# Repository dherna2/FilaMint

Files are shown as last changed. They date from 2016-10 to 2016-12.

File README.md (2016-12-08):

# FilaMint Team4

## This github was created for ECE411 Practicum Fall 2016  

### Collaborators are:

Colleen Nhim  
Nettaly Rebolledo  
David Hernandez  
Srijana Sapkota  

We used [Google drive] to simultanelously work on documents.  
Our finished documents have been transferred to the [Wiki](../../wiki) or saved in the folder named documents. 

[Google drive]: https://drive.google.com/drive/u/1/folders/0B7ei5UTStXl6bGFZWWxhMDdIQzQ

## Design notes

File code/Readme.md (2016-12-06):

Notes about wire connections to arduino, sensors with boards and prototype/Filamint board.  

gnd: hum(furthest pin right with holes facing up next to empty pin), lcd ("G" written on LCD board)

5v: hum(furthest pin left with holes facing up next to signal pin) , lcd ("P" written on LCD board)

Arduino 2 - hum_sig-resistor (2nd pin from left with holes facing up) - 328p pin4  
Note prototype is model after board which has digital pin 0 and 2 shorted

Arduino 8 - HX711 SCK -  328p pin14  

Arduino A3 - HX711 data - 328p pin26  

Arduino A5 - SCL ("L" written on LCD board) - 328p pin28 

Arduino A4 - SDA ("D" written on LCD board) - 328p pin27

Also Need to have the library for LCD installed, adafruit sensors, HX711  

Note for filamint board connectors have + for vcc and - for gnd helps with connector orientation

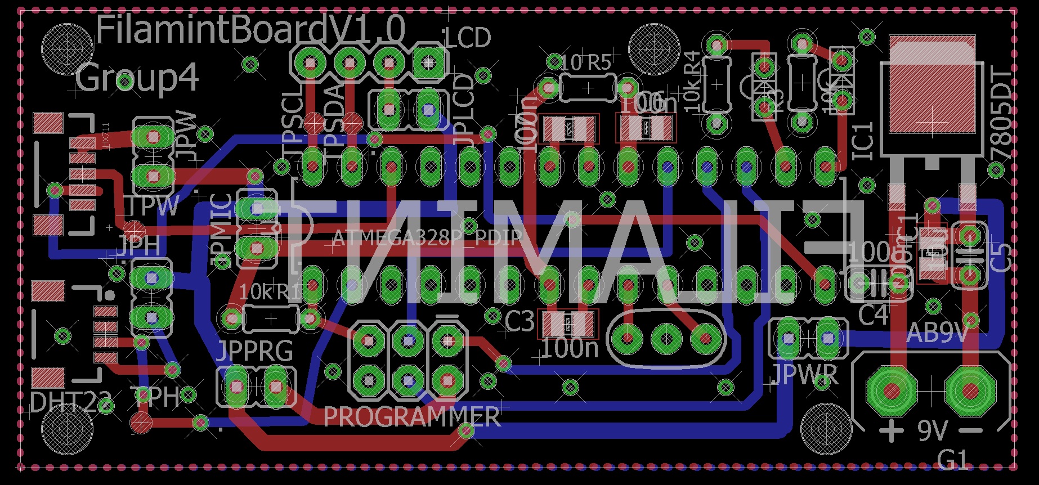
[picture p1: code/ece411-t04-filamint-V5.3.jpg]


[logo]: https://github.com/dherna2/FilaMint/blob/master/code/ece411-t04-filamint-V5.3.jpg "Homer is awsome"

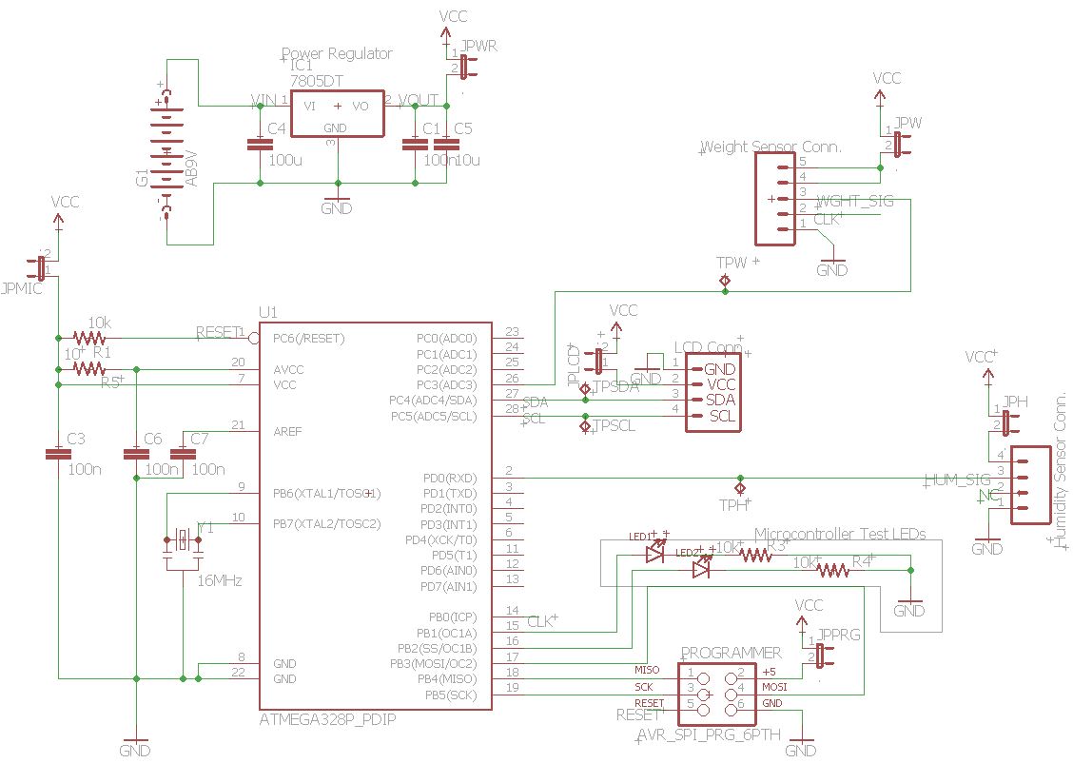
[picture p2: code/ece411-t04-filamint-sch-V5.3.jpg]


[logo2]: https://github.com/dherna2/FilaMint/blob/master/code/ece411-t04-filamint-sch-V5.3.jpg "Homer is awsome"

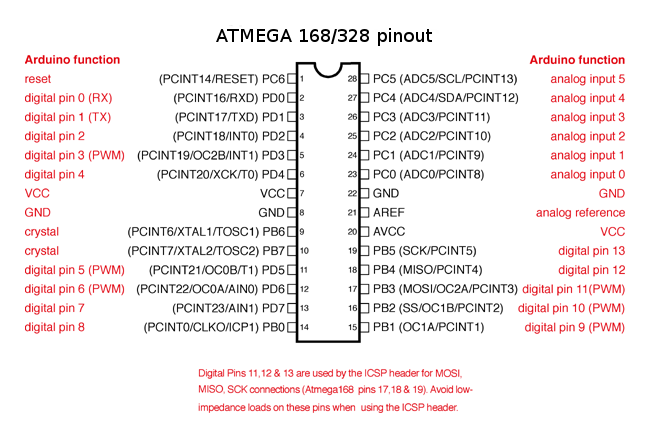
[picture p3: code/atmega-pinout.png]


[logo3]: https://github.com/dherna2/FilaMint/blob/master/code/atmega-pinout.png "Homer is awsome"

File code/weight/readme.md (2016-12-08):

## hx711 board connection  

The four wires coming out from the wheatstone bridge on the load cell are usually:  
•Excitation+ (E+) or VCC is red  
•Excitation- (E-) or ground is black  
•A-, O- or S- is green or blue  
•Amplifier+ (A+), Output+ (O+) or Signal+ (S+) is white

HX711 board -> Arduino 
GND-> GND  
DT->A1  
SCK->A0  
VCC-> 5v

Need to save this folder into your arduino library folder dont need test folder.
[Load Cell Library Source bogde](https://github.com/bogde/HX711)

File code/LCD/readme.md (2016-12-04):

## Wire Connection  

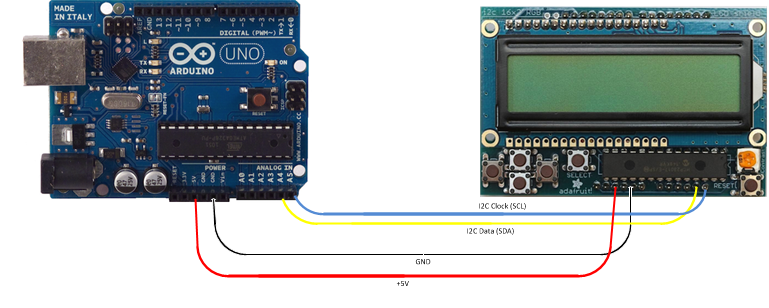
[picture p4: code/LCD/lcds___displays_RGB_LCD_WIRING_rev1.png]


[logo]: https://github.com/dherna2/FilaMint/blob/master/code/LCD/lcds___displays_RGB_LCD_WIRING_rev1.png "Homer is awsome"

Need to unzip file and save it in your arduino library folder  

Further details on use see adafruit tutorial [Using the RGB LCD Shield](https://learn.adafruit.com/rgb-lcd-shield/using-the-rgb-lcd-shield)

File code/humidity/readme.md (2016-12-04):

## Wire Connection  

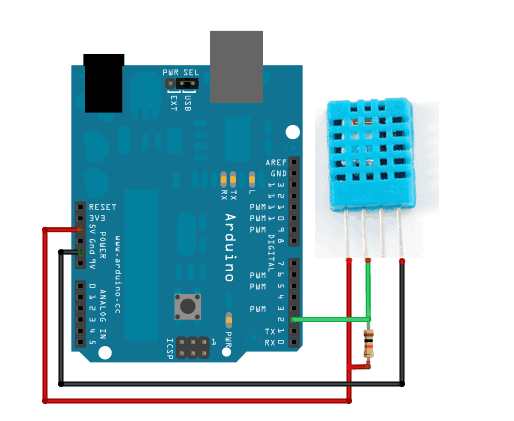
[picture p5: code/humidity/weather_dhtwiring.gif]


[logo]: https://github.com/dherna2/FilaMint/blob/master/code/humidity/weather_dhtwiring.gif "Homer is awsome"

Need to unzip both files and save them in your arduino library folder  

Further details on use see adafruit tutorial [Using a DHTxx Sensor](https://learn.adafruit.com/dht/using-a-dhtxx-sensor)

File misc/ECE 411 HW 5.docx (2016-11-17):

ECE 411

Homework 5

Group 4

# UML Physical View

→ → →

## USER

Box

Fridge

Nurse

## COMMUNICATION

## DATABASE

Compare values against server

Store values

Temp

ID/Patient/Vaccine

Date

## SERVER

Alarm text

UML Case Description

Use-Case | Activate temperature sensor
Actors | Customer, database, server
Description | The use-case occurs when a new temperature sensor is installed. Once installed, the server prompts the customer to add information, and check whether they have a subscription. If they don’t, the server prompts for payment information. If they do, then the sensor gets activated.
Stimulus | Costumer purchases a new sensor, then installs it into the fridge.
Response | Verify information, trigger monitor.

# UML Interaction View

5) Notify

Database

Sensor

Server

Comm

1) Wake up 3) Inquire →
2) Check temp → 4) Validity →

# HTTP GET String

http://www.vaccine.com/test/tempr_form.asp?name1=filamint_clinic&temp=98

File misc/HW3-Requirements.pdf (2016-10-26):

# FilaMint Requirements

# Group 4

## ECE 411 Version 2.0

FilaMint | 1

## Need

Filament is often improperly stored, which exposes the material to moisture. This exposure to moisture deteriorates the quality of the filament, therefore deteriorating the quality of the user’s print job. Additionally, printers normally will tell you how much filament has been used, but there is usually no way for the printer to measure how much filament is remaining on the spool. Both these issues lead to printing failures. There had to be a solution to fix these common issues for 3D printing enthusiasts. Because this market is starting to become affordable to all, FilaMint was created to become the affordable solution.

## Objective

The objective is to create an inexpensive device that will alert the customer if the storage humidity level is too high as well as when the filament is running low. The system must monitor humidity, alert user if humidity is too high, securely store filament in the enclosed and sealed container, and estimate how much filament is remaining.

## Background

A simple google search has shown that there have been similar designs that were created to prevent humidity from getting into the filament, but none that incorporate humidity and weight measurements in the same design. Some designs used a modified ‘air tight storage tote’ or a large ziplock bag that was then vacuum sealed. These designs were very low cost but didn’t alarm when humidity levels were too high. Some more expensive designs ($150+) looked like a modified desiccator oven that fits filament spools and it was able to regenerate desiccant packs, but this design did not monitor humidity levels or alarms. None of these designs measured the weight of the filament either.

## Requirements

### Functionality

- System must detect humidity within the container and alert the user if humidity is too high
- System must measure weight of the filament and alert the user if the filament is too low
- System must have an interface so the user can select type of filament they are storing
- The container must be sealed in order to reduce humidity

### Performance

- The weight measurement accuracy must be within 1 gram at all times
- The humidity sensor accuracy must be within 5% at all times
- The container must be able to store at least one spool of filament
- Information must be visible within 5 seconds when prompted

### Manufacturability

- The system must be manufactured on a circuit board with linear dimensions no less than 2cm and not greater than 30cm
- The system must be manufactured using two-layer printed circuit board technology

### Operational

- The system must be able to be able to operate in typical indoor environments (non-extreme).
- Must be used on a flat surface

### Economic

- Unit cost of less than $150
- Affordable unit
- The only maintenance cost must be the replacement of batteries.
- Must maintain silica beads

### Energy

- Must have replaceable power supply
- Supply must last a minimum of a month on standby

### Health & Safety

- Must not explode
- Must not emit unhealthy amounts of radiation
- System must not exceed ten pounds

### Legal

- Non-infringing patents and copyrights

### Environmental

- At least 50% of the components will be recyclable

### Maintainability

- User maintainable
- Product hardware components can be bought from at least 2 vendors

### Reliability & Availability

- MTTF 5 years

### Social & Cultural

- Must be easy to use and maintain by technical and non-technical users
- Intuitive and self-explaining

### Usability

- No on-site or user customization necessary or programming
- No longer than 30 minutes to learn how to use product
- Straightforward user interface with no more than 5 levels of menu options

### Documentation

- Instructions on the side explaining how to replace or recharge silica beads
- Instructions on how to use product

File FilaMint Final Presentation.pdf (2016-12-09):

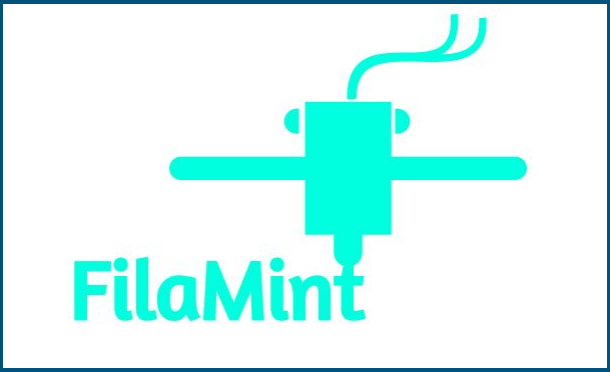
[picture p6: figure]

Portland State University
Group 4
Colleen Nhim, David Hernandez, Nettaly Rebolledo, Srijana Sapkota

# Background

# Solution

Project We wanted to create a product that would safely store filament in a way that prevent exposure to moisture. Warnings for high humidity and low filament.

Importance Keeping filament unexposed to moisture will preserve the quality of the filament, therefore maintaining the quality of the print job and success rate. The product will also let the user know how much filament is remaining so they are not risking the chances of running out of filament mid print. This product is crucial to successful print jobs.

# Objective

Filament is often kept unstored leaving exposure to moisture. Printers tell you how much you’ve printed but not how much filament is left in a spool. This product fixes both of these issues to increase the success and quality of a print job.

Our goal is to create a working prototype to pair with a 3D printer.

# Alternatives

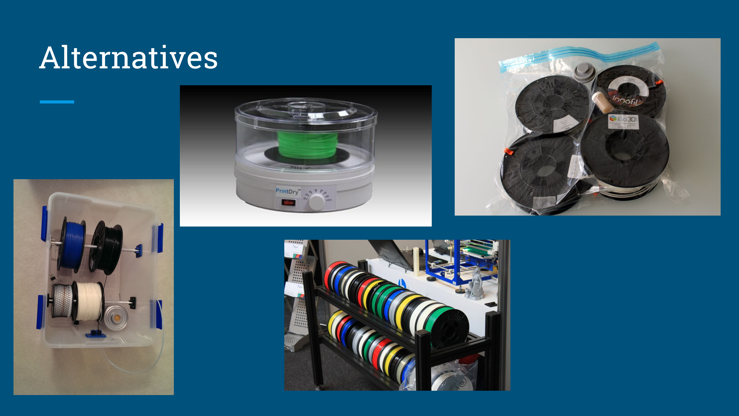
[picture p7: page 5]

# Requirements

## Functionality

- System must detect humidity within the container and alert the user if humidity is too high
- System must measure the length of the filament and alert the user if the filament is too low
- System must have an interface so they can get the readings from the container
- The container must be sealed in order to reduce humidity

# Requirements

## Performance

- The weight measurement accuracy must be within 1 gram at all times
- The humidity sensor accuracy must be within 5% at all times
- The container must be able to store at least one spool of filament
- Information must be visible within 5 seconds when prompted

# Approach

-Wanted to be cost effective

-Not take up a lot of space

-Accurate measurements and calculations

# Design: Hardware

# Black Box

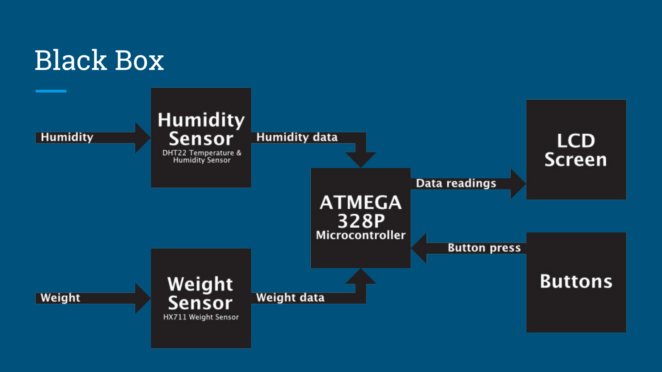
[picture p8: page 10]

# Event Table

EVENT | TRIGGER | PROCESS | SOURCE
Display readings | Button press | Data read | User
High humidity alert | Humidity readings | Display alert on LCD screen | System
Low filament warning | Remaining length reading | Display alert on LCD screen | System

# Hardware

1. Load cell - weight sensor
- To measure weight of filament spool
- Load cell is a transducer that translates force/ pressure into electric signal.
- Bar Strain gauges: Two wired organized wires where resistance changes upon stretching/ compressing
- Force sensed by deformation of strain gauge(s)
- Bar strain gauge load cell (Z-shape) (provides torque for easier and accurate measurement)

# Hardware

2. HX711 - Load cell Amplifier breakout board
- Load cell amplifier to read load cells to measure weight.
- Reads in small change in resistance and we can measure accurate weight with some calibration.
- Wheatstone bridge configuration used by load cell to connect to HX711
- Load cell has 4 strain gauges hooked up in wheatstone bridge formation (takes small change in resistance and make it more measurable)

# Hardware

3. DHT22 - Humidity Sensor
- Low cost temperature and humidity sensor
- Uses capacitive humidity sensor to measure surrounding air
- Use pullup resistor from data pin to Vcc.

# Hardware

4. LCD
- LCD Shield Kit w/ 16x2 Character Display
- I2C communication uses only 2 pins to connect with microcontroller
- 5 keypad buttons built-in the LCD
- Blue and White colors
- Backlight

# Hardware

5. ATMega328P-PU - Microcontroller and SMD components
- Low cost microcontroller
- Similar to Arduino Uno - used for Development
- 8 bit AVR, 32 ch, 23 GPIO
- External 16 MHz Resonator with Built in Capacitor
- 100nF SMD Capacitor in 805 packaging
- LM340S Line 5v Voltage Regulator
- 4 pin SMD connector and ribbon cables

# Design: Software

Software and Misc.

C - Language using Arduino

- Humidity and LCD libraries were downloaded from purchaser Adafruit.
- HX711 library was downloaded from github after finding one that worked
- Combined the examples together to form our code

Misc

- ¼ in. Acrylic sheets for support and durability
- 4xAA battery holder to provide long life

# Implementation

# Components

-Humidity Sensor: Analog to digital humidity and temperature sensor

-Weight Sensor: Weighs the spool

-Microcontroller: Controls the circuit

-LCD Display: Displays readings and menu

-Acrylic: The container

-Silica beads: Used to maintain low humidity levels

-Plexiglass: Sheets put together to make shell

# Bill of Materials

Part | Quantity | Price (including shipping)
Microprocessor | 1 | $5.00
Humidity Sensor | 1 | $7.00
Blue and White LCD kit | 1 | $25.00
4xAA Battery Pack | 1 | $2.92
HX711 Board | 1 | $2.93
Plexiglass sheets ($9 ea) | 3 | $27.00
Misc hardware (i.e. screws, hinges, etc) | 1 | $10.00
| | Total: $79.85

# Tools Used

- Arduino used for Development
- Eagle CAD used for schematic and board layout
- Laser cutter for plexiglass
- Drill press for screw holes

# Test Cases

Test Case Link (https://docs.google.com/a/pdx.edu/spreadsheets/d/1ZcRj_BzytFNqw8m9PkoywJ23xHQr0xwOn_bJI6cZJ2M/edit?usp=sharing)

# Schematic

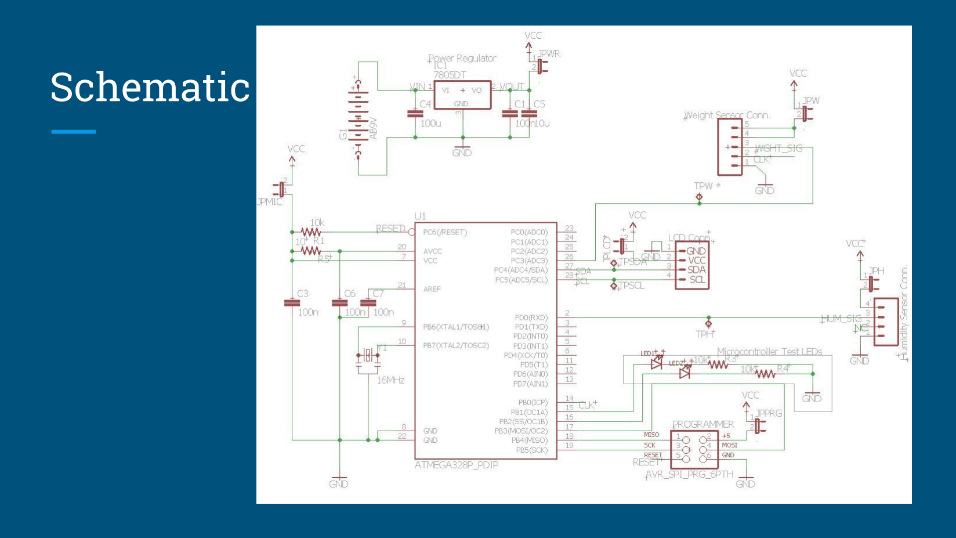
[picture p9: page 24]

# Board Layout

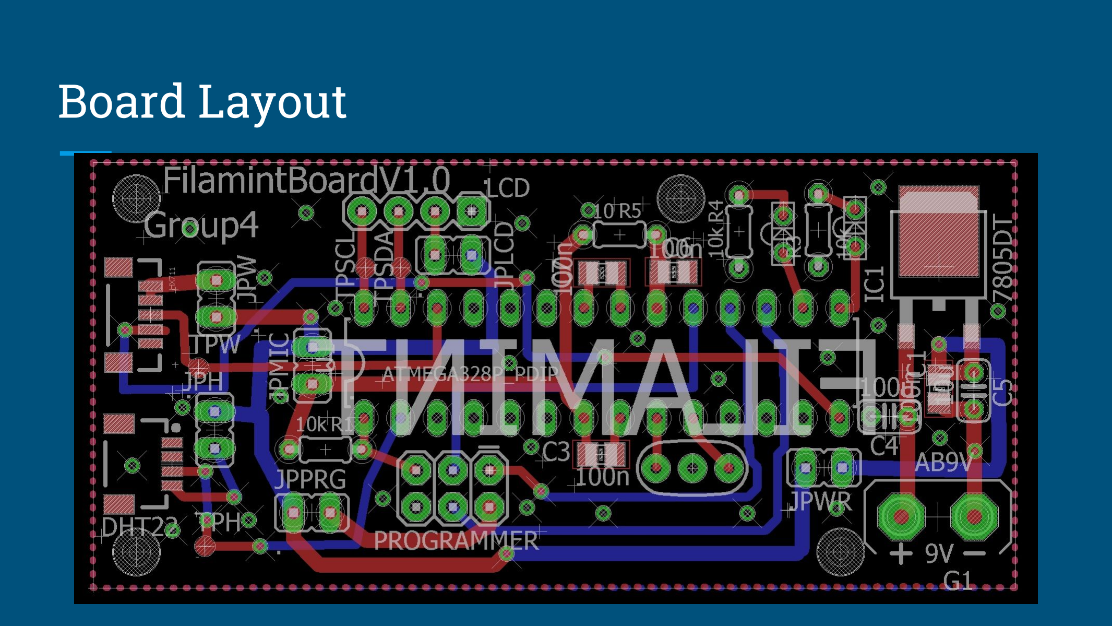
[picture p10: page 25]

# Prototype Board

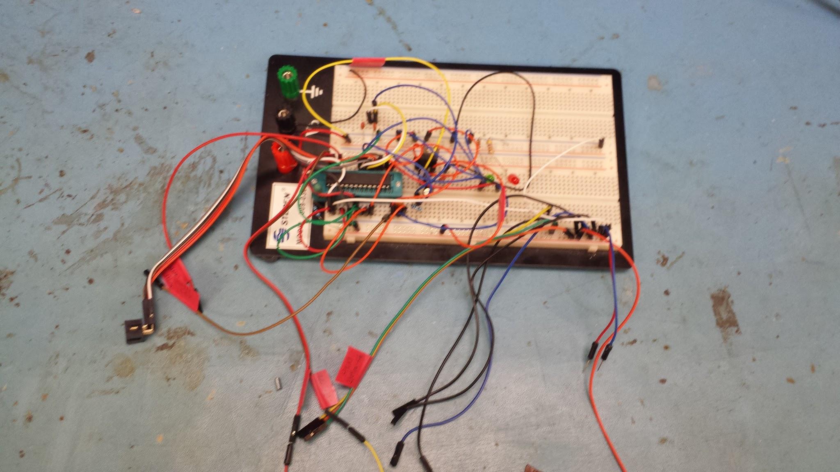
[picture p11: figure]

# Code

-Mass to Length conversion equation

-User Interface menu

-Displays and warns of high levels of humidity and low filament length

# Code

- Github (https://github.com/dherna2/FilaMint/blob/master/code/filamint_code/FilaMintVer12.ino)

# IP and Prior Work

# Referenced Work

- Used purchaser’s Libraries, example code and tutorials
- LCD - Adafruit
- Humidity - Adafruit
- Weight - open source code from github user bogde

# Testing

# Strategy for Testing

- Solder board and parts together
- Upload code to board
- Debug

# Results

# What worked?

- Team meetings - accomplished a lot together in a short amount of time
- Google Drive to simultaneously work on documents
- GitHub to share code, create helpful pages, and revision control
- Locker with easy to remember combo “MINT” to keep all items at school
- Google Hangouts to create a dedicated group chat with all members this helped with status reports, questions, tips, notes, accountability
- LID and capstone lab tools i.e. laser cutter, drill press, crimper, dremel, etc.
- Extra parts purchased (we got some bad parts and slow shipping)

# What didn’t work?

- Example codes - found out some example codes were outdated
- SMD connectors and ribbon cables are difficult to work with
- Group decisions on small items took longer than expected
- Learning curve was long for new tools i.e. github, eagle cad, arduino, atmel_studio, SMD soldering, LID tools-laser cutter, reflow oven

# Individual Contributions

Colleen: coding, laser cutting, assembly, calculations/conversions, filament

David: construction, assembly, coding, debugging, EagleCAD design

Nettaly: debugging, coding, design, circuit analysis

Srijana: board layout, assembly, coding, laser cut, documentation

# Lessons Learned

-What did each member learn

-what would we do differently

- More peer reviews
- Dedicated roles with backup
- More communication

-If we had more time…

- Better menu

-biggest mistake

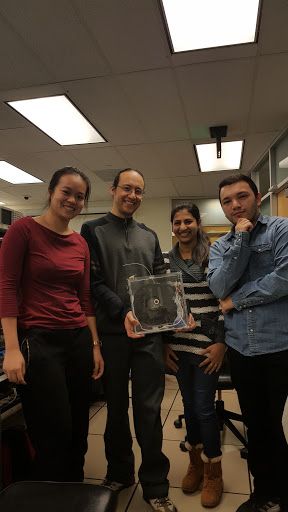
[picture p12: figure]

# Live demonstration!!

Thank you!

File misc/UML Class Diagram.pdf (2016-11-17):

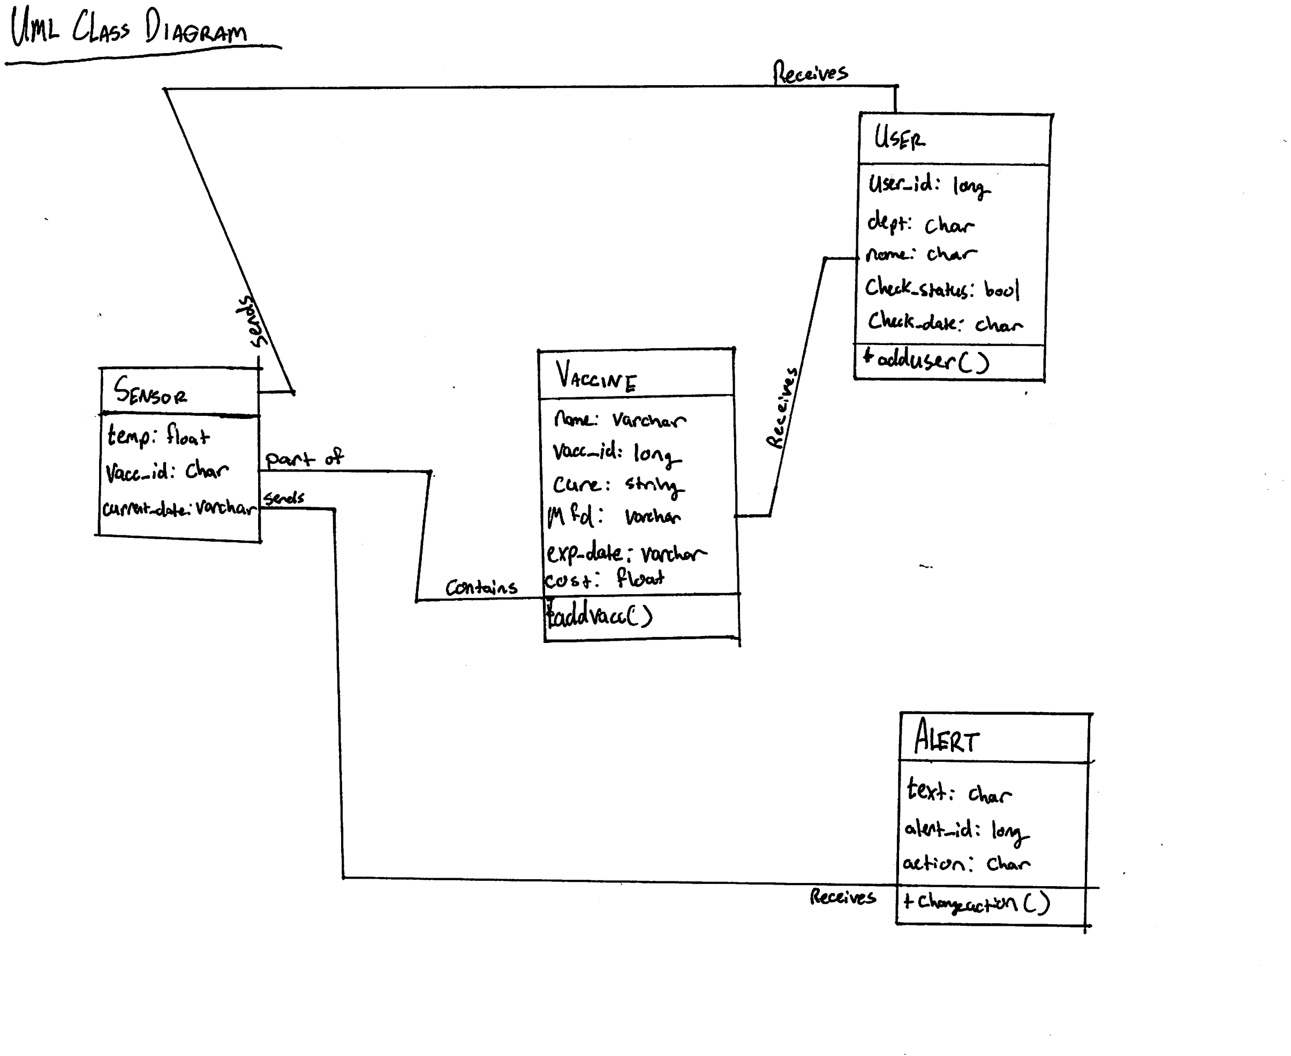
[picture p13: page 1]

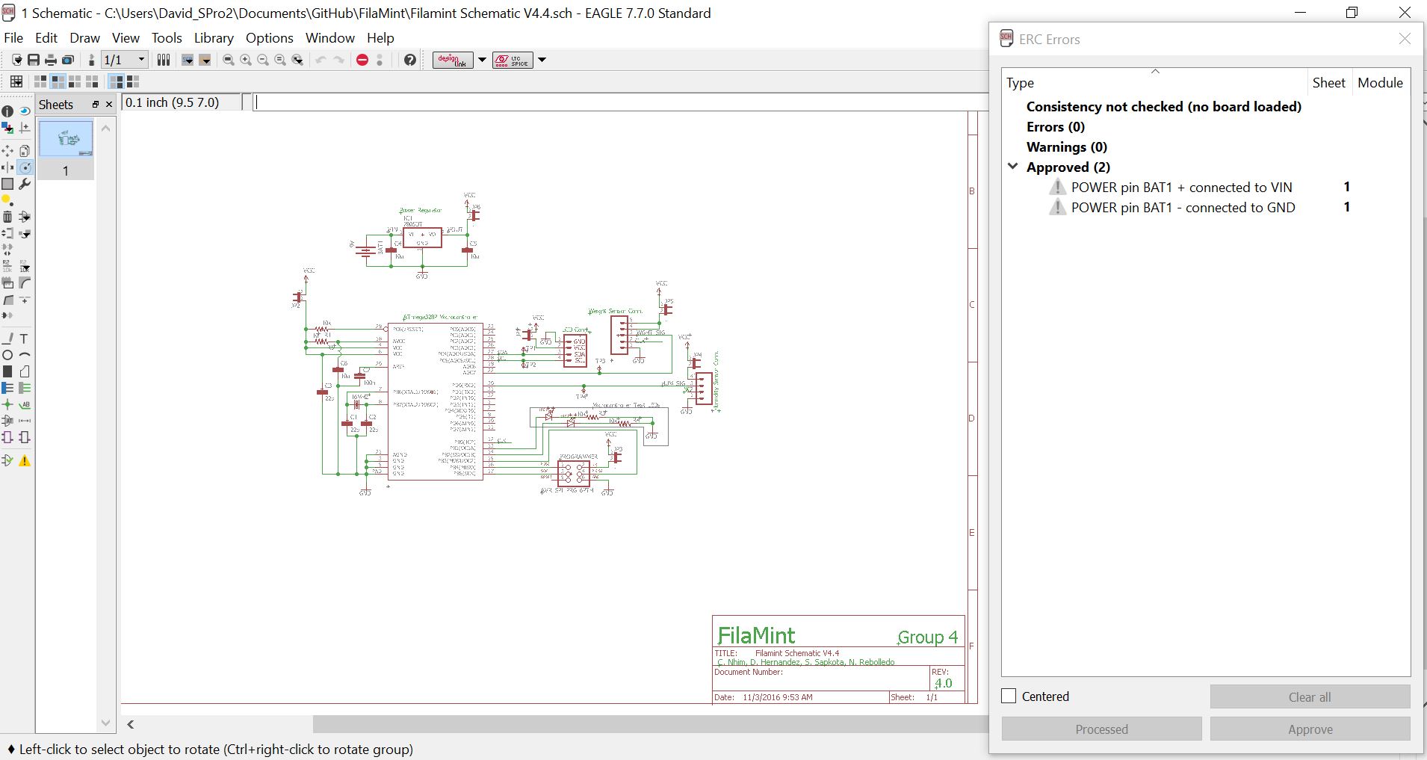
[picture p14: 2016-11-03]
Schematic/Filamint Schematic V4.4_ERC.JPG

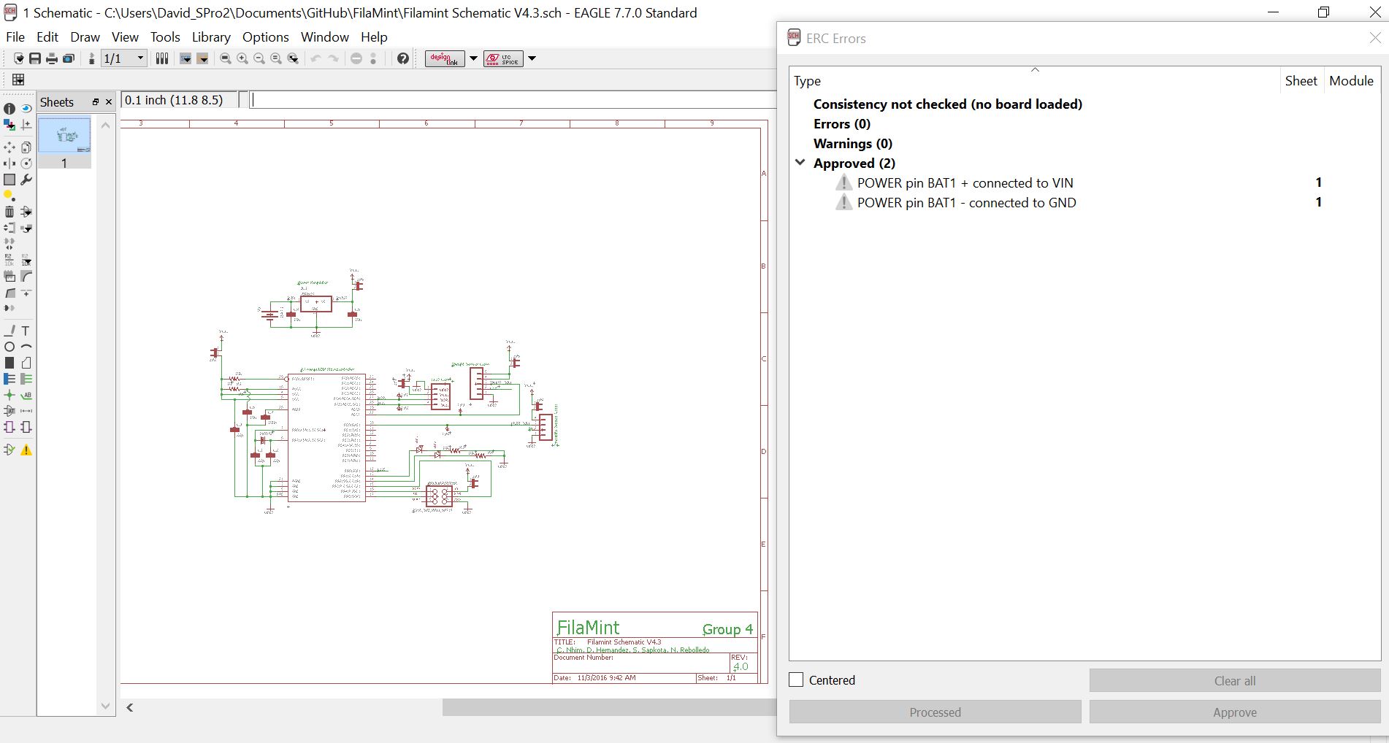
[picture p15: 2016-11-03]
Schematic/Filamint Schematic V4.3_ERC.JPG

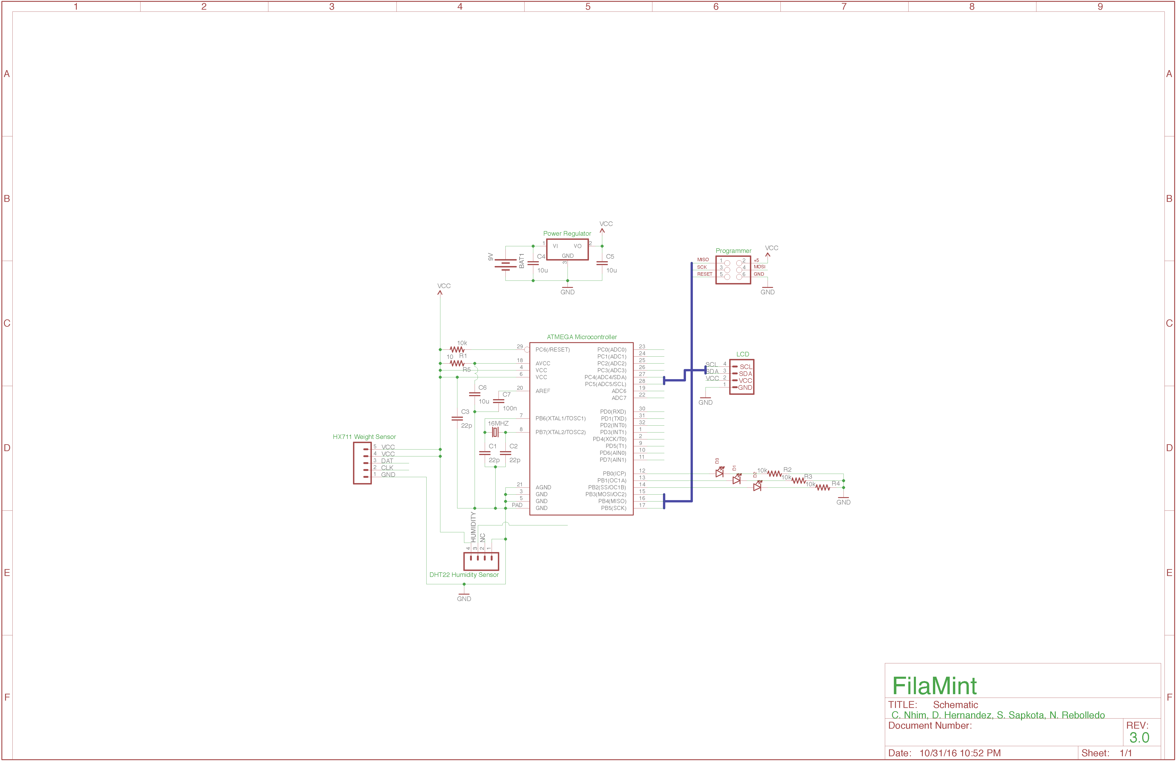
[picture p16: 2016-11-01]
Schematic/Filamint Schematic.png

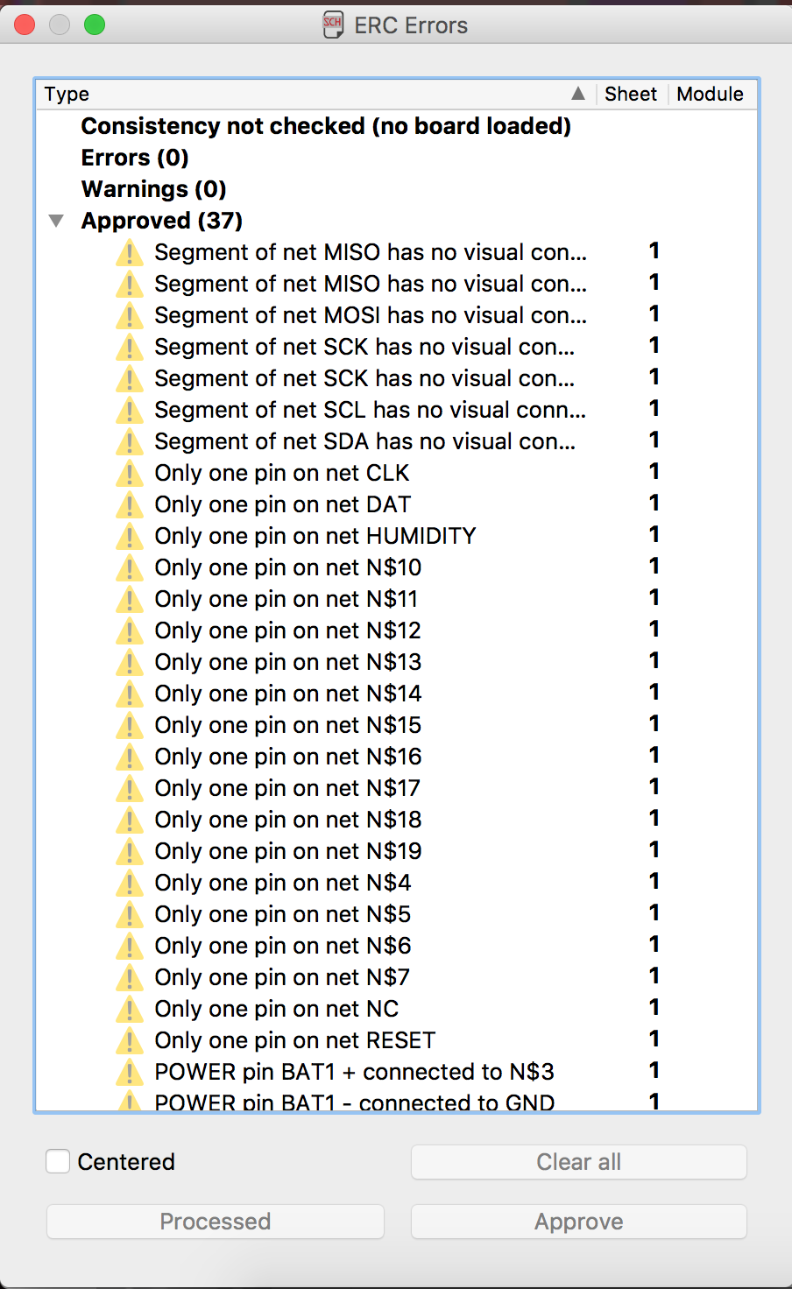
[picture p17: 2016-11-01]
Schematic/ERC Screen1.png

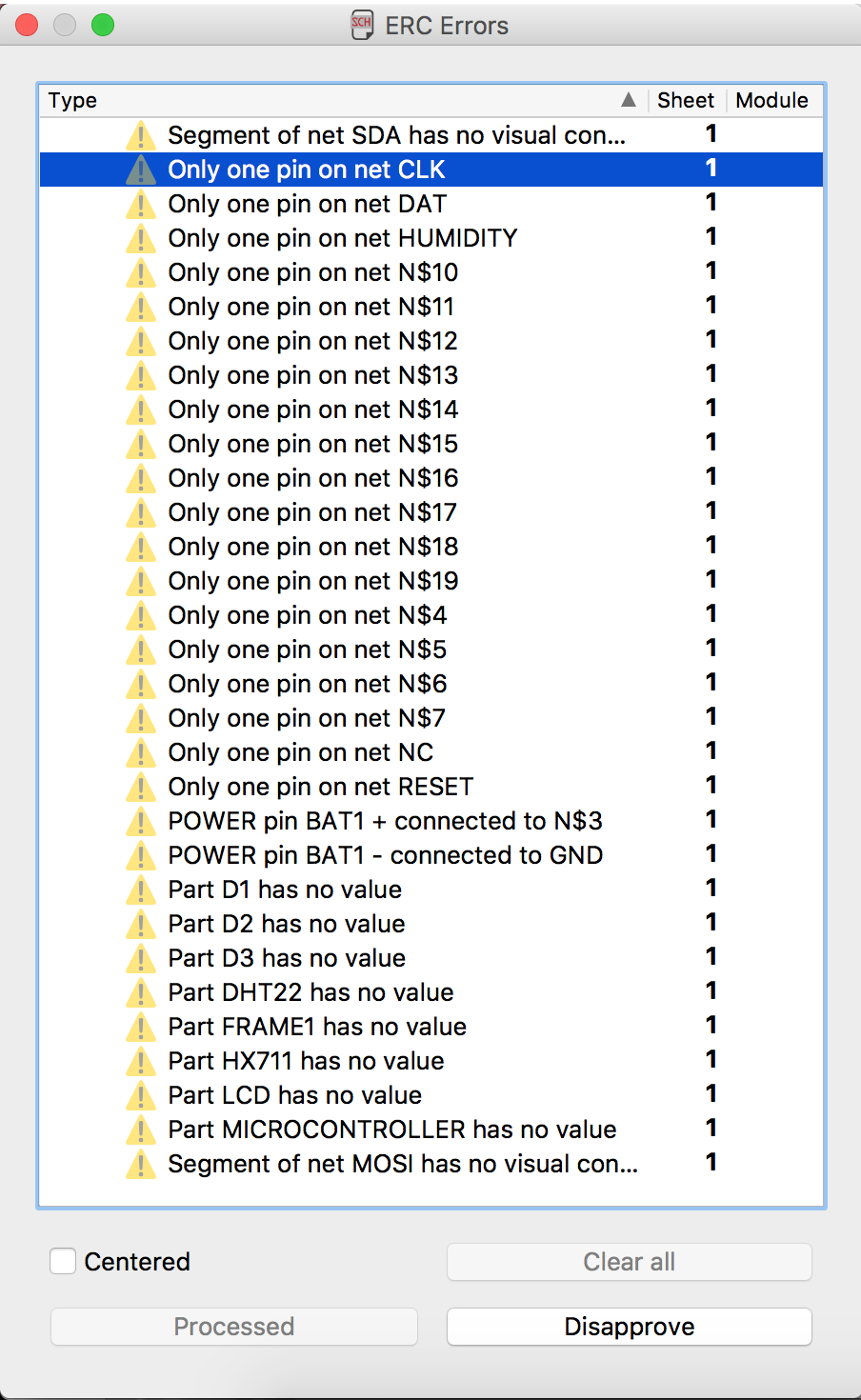
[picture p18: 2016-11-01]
Schematic/ERC Screen 3.png

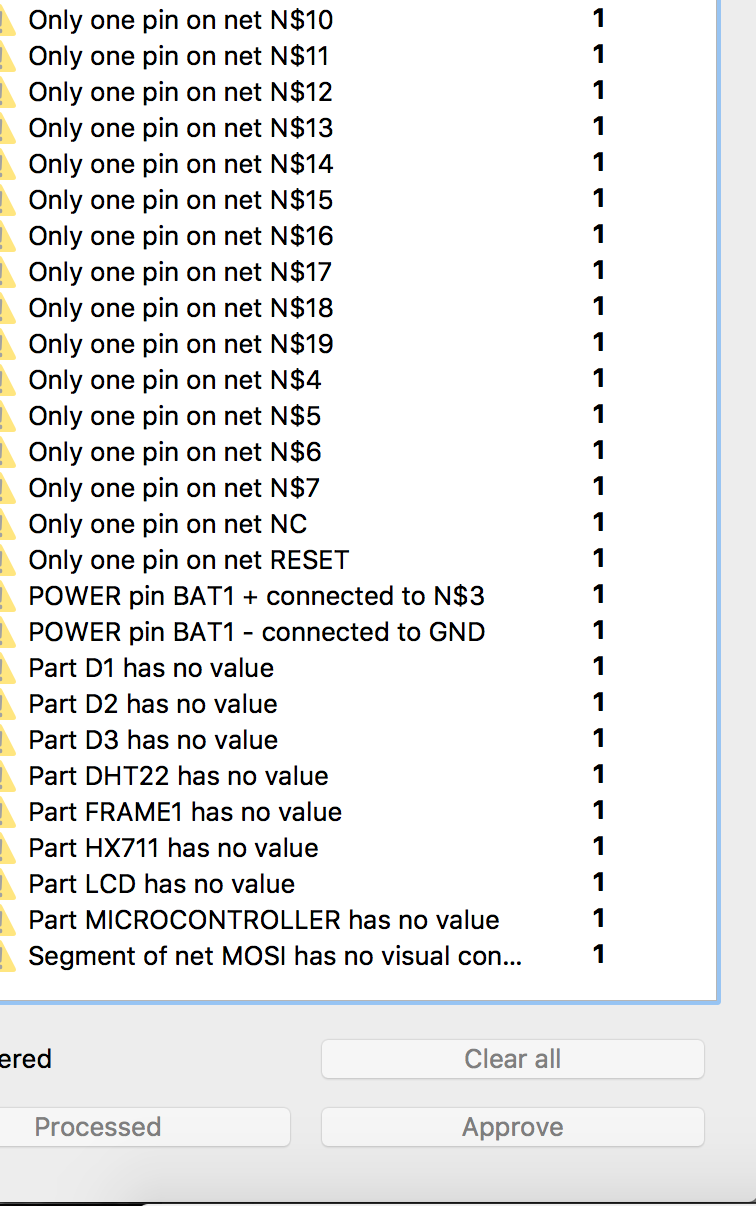
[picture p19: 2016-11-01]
Schematic/ERC Screen 2.png

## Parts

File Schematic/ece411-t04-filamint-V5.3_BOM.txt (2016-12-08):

Partlist exported from C:/Users/David_desk/Documents/eagle/ece411-t04-filamint-V5.3.sch at 11/28/2016 12:37 PM

Qty Value            Device           Package       Parts                               Description                                                               TP_SIGNAL_NAME
1   .                I2C_STANDARD     1X04          LCD                                 SparkFun has standardized on a pinout for all I2C based sensor breakouts.               
6   .                JP1E             JP1           JPH, JPLCD, JPMIC, JPPRG, JPW, JPWR JUMPER                                                                                  
2   .                LTE-302          LTE-302       LED1, LED2                          Through-hole side-firing 940nm IR LED                                                   
1   .                M04SMD2          1X04-1MM-RA   DHT22                               Header 4                                                                                
1   .                M05SMD           1X05-1MM      HX711                               Header 5                                                                                
1   10               R-US_0204/5      0204/5        R5                                  RESISTOR, American symbol                                                               
4   100n             C-EUC0805        C0805         C1, C3, C6, C7                      CAPACITOR, European symbol                                                              
1   100u             C-EU025-024X044  C025-024X044  C4                                  CAPACITOR, European symbol                                                              
3   10k              R-US_0204/5      0204/5        R1, R3, R4                          RESISTOR, American symbol                                                               
1   10u              C-EU025-024X044  C025-024X044  C5                                  CAPACITOR, European symbol                                                              
1   16MHz            RESONATORPTH     RESONATOR-PTH Y1                                  Resonator                                                                               
1   7805DT           7805DT           TO252         IC1                                 Positive VOLTAGE REGULATOR                                                              
1   AB9V             AB9V             AB9V          G1                                  9-V BATTERY CLIP                                                                        
1   ATMEGA328P_PDIP  ATMEGA328P_PDIP  DIL28-3       U1                                  uC used in the Arduino                                                                  
1   AVR_SPI_PRG_6PTH AVR_SPI_PRG_6PTH 2X3           PROGRAMMER                          AVR ISP 6 Pin                                                                           
4   TPB1,27          TPB1,27          B1,27         TPH, TPSCL, TPSDA, TPW              Test pad

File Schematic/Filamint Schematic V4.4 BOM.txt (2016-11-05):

Partlist exported from C:/Users/David_SPro2/Documents/GitHub/FilaMint/Filamint Schematic V4.4.sch at 11/3/2016 9:55 AM

Part            Value            Device              Package      Description                                                               MF MPN OC_FARNELL OC_NEWARK TP_SIGNAL_NAME
16MHZ           CSM-7X-DU        CSM-7X-DU           CSM-7X-DU    SMD CRYSTAL                                                                      unknown    unknown                 
BAT1            9V               BATTERY9V           BATTCON_9V   Battery Holders                                                                                                     
C1              22p              C-EU025-024X044     C025-024X044 CAPACITOR, European symbol                                                                                          
C2              22p              C-EU025-024X044     C025-024X044 CAPACITOR, European symbol                                                                                          
C3              22p              C-EU025-024X044     C025-024X044 CAPACITOR, European symbol                                                                                          
C4              10u              C-EU025-024X044     C025-024X044 CAPACITOR, European symbol                                                                                          
C5              10u              C-EU025-024X044     C025-024X044 CAPACITOR, European symbol                                                                                          
C6              10u              C-EU025-024X044     C025-024X044 CAPACITOR, European symbol                                                                                          
C7              100n             C-EU025-024X044     C025-024X044 CAPACITOR, European symbol                                                                                          
DHT22           .                M04SMD2             1X04-1MM-RA  Header 4                                                                                                            
HX711           .                M05SMD              1X05-1MM     Header 5                                                                                                            
IC1             7805DT           7805DT              TO252        Positive VOLTAGE REGULATOR                                                                                          
JP1             .                JP1E                JP1          JUMPER                                                                                                              
JP2             .                JP1E                JP1          JUMPER                                                                                                              
JP3             .                JP1E                JP1          JUMPER                                                                                                              
JP4             .                JP1E                JP1          JUMPER                                                                                                              
JP5             .                JP1E                JP1          JUMPER                                                                                                              
JP6             .                JP1E                JP1          JUMPER                                                                                                              
LCD             .                I2C_STANDARD        1X04         SparkFun has standardized on a pinout for all I2C based sensor breakouts.                                           
LED1            .                LTE-302             LTE-302      Through-hole side-firing 940nm IR LED                                                                               
LED2            .                LTE-302             LTE-302      Through-hole side-firing 940nm IR LED                                                                               
MICROCONTROLLER .                ATMEGA328P_MLFMLF32 MLF32-PAD    32-Pin Atmega328 part                                                                                               
PROGRAMMER      AVR_SPI_PRG_6PTH AVR_SPI_PRG_6PTH    2X3          AVR ISP 6 Pin                                                                                                       
R1              10k              R-US_0204/5         0204/5       RESISTOR, American symbol                                                                                           
R3              10k              R-US_0204/5         0204/5       RESISTOR, American symbol                                                                                           
R4              10k              R-US_0204/5         0204/5       RESISTOR, American symbol                                                                                           
R5              10               R-US_0204/5         0204/5       RESISTOR, American symbol                                                                                           
TP1             TPB1,27          TPB1,27             B1,27        Test pad                                                                                                            
TP2             TPB1,27          TPB1,27             B1,27        Test pad                                                                                                            
TP3             TPB1,27          TPB1,27             B1,27        Test pad                                                                                                            
TP4             TPB1,27          TPB1,27             B1,27        Test pad

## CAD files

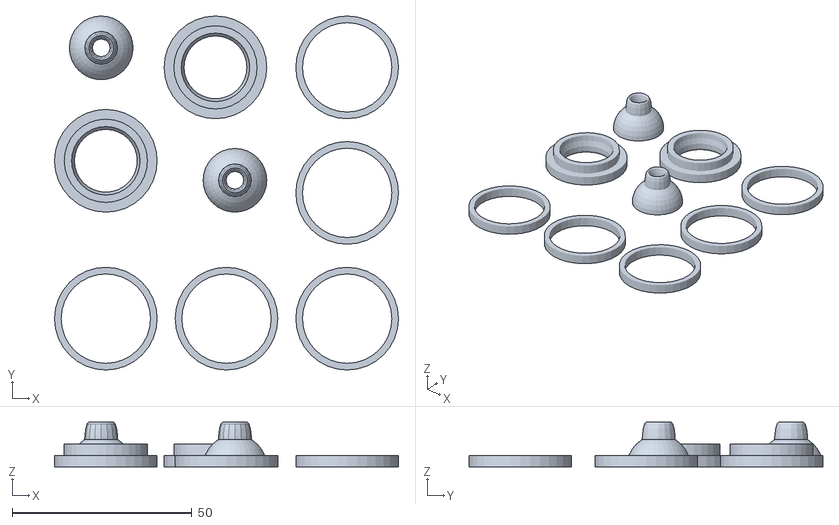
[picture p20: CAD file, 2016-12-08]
misc/thru-swivel_with_rings.stl
95.7 x 98.5 x 12.4

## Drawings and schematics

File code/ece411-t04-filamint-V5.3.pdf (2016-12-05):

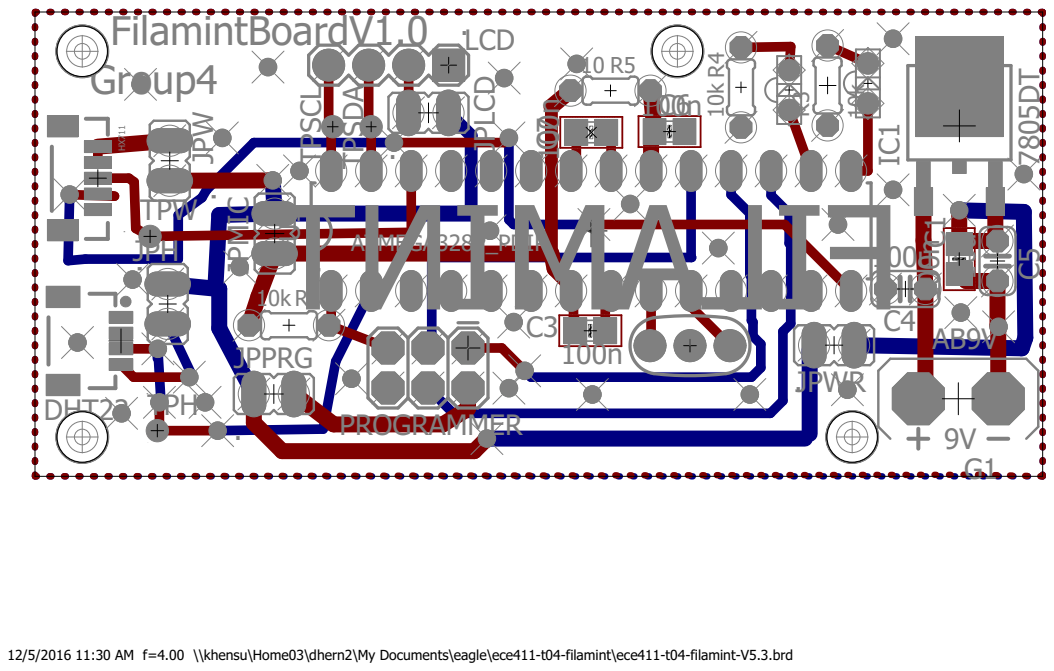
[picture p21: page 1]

12/5/2016 11:30 AM f=4.00 \\khensu\Home03\dhern2\My Documents\eagle\ece411-t04-filamint\ece411-t04-filamint-V5.3.brd

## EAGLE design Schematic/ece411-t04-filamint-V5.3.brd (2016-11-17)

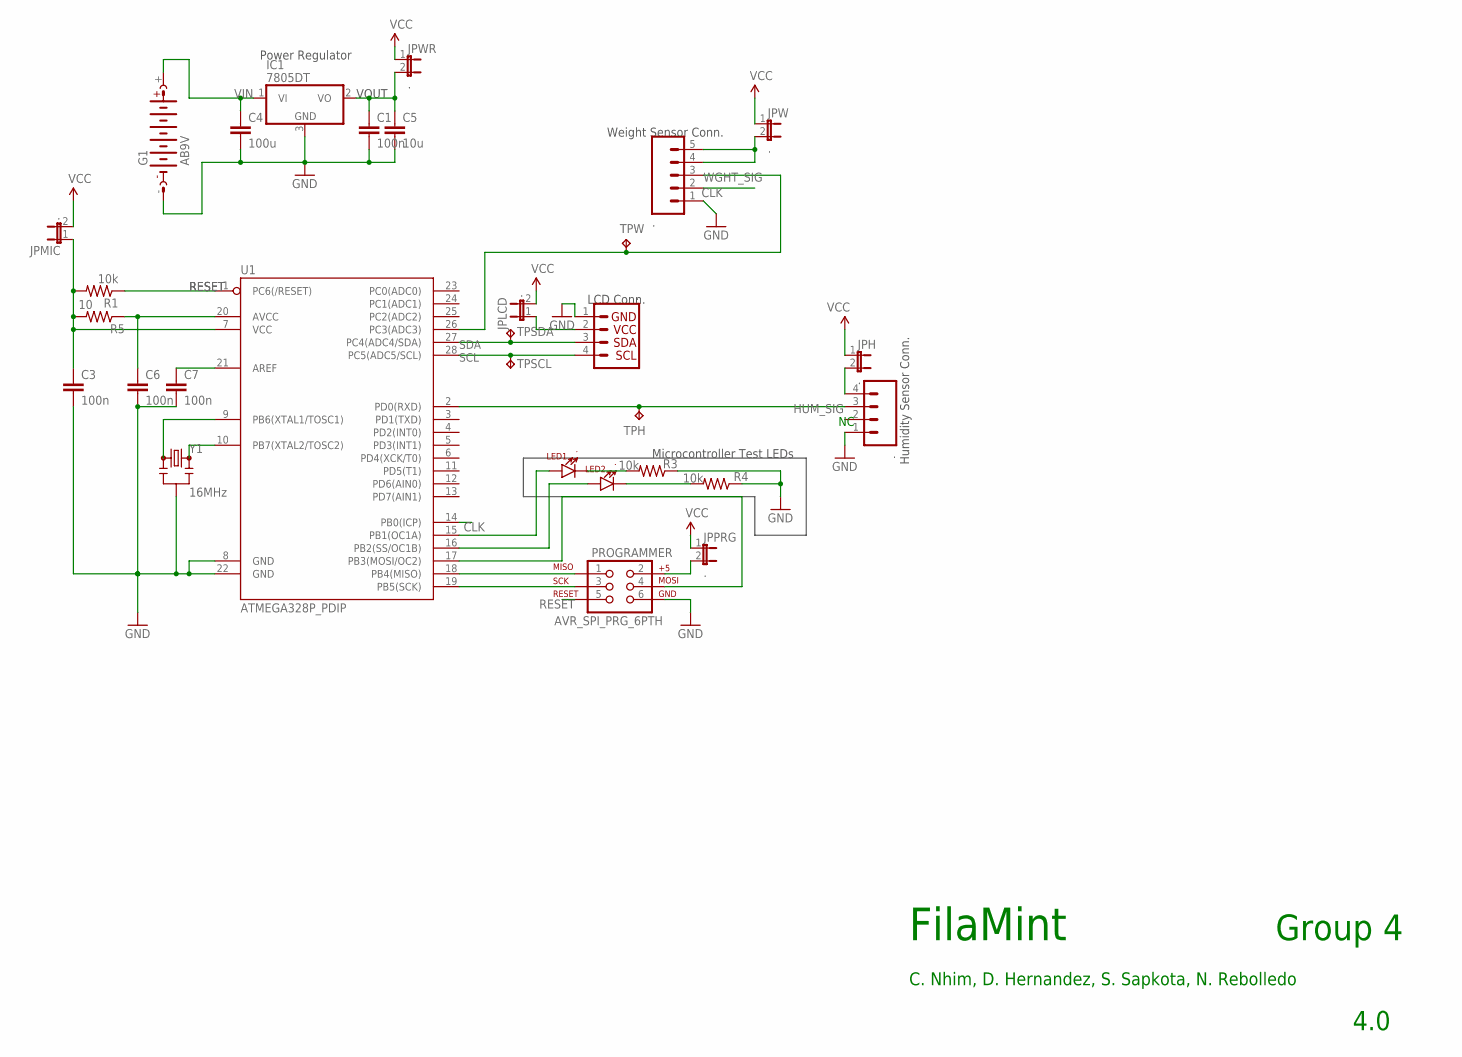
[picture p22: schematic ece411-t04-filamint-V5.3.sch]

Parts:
C1, C3, C6, C7: 100n; C0805
C4: 100u; C025-024X044
C5: 10u; C025-024X044
DHT22: .; 1X04-1MM-RA
G1: AB9V
HX711: .; 1X05-1MM
IC1: 7805DT; TO252
JPH: .; JP1
JPLCD: .; JP1
JPMIC: .; JP1
JPPRG: .; JP1
JPW: .; JP1
JPWR: .; JP1
LCD: .; 1X04
LED1, LED2: .; LTE-302
PROGRAMMER: AVR_SPI_PRG_6PTH; 2X3
R1, R3, R4: 10k; 0204/5
R5: 10; 0204/5
TPH: TPB1,27; B1,27
TPSCL: TPB1,27; B1,27
TPSDA: TPB1,27; B1,27
TPW: TPB1,27; B1,27
U1: ATMEGA328P_PDIP; DIL28-3
Y1: 16MHz; RESONATOR-PTH

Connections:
AVCC: C6.1, R5.1, U1.20 (AVCC)
CLK: HX711.2, U1.14 (PB0(ICP))
GND: C1.2, C3.2, C4.2, C5.2, C6.2, C7.2, DHT22.1, G1.-, HX711.1, IC1.3 (GND), LCD.1, PROGRAMMER.6, R3.1, R4.1, U1.8 (GND), U1.22 (GND), Y1.2
HUM_SIG: DHT22.3, TPH.TP, U1.2 (PD0(RXD))
MISO: PROGRAMMER.1, U1.18 (PB4(MISO))
MOSI: PROGRAMMER.4, U1.17 (PB3(MOSI/OC2))
unnamed: U1.9 (PB6(XTAL1/TOSC1)), Y1.1
unnamed: U1.10 (PB7(XTAL2/TOSC2)), Y1.3
unnamed: HX711.4, HX711.5, JPW.2
unnamed: C7.1, U1.21 (AREF)
unnamed: LED1.A, U1.15 (PB1(OC1A))
unnamed: LED2.A, U1.16 (PB2(SS/OC1B))
unnamed: DHT22.4, JPH.2
unnamed: LED1.C, R3.2
unnamed: LED2.C, R4.2
unnamed: JPPRG.2, PROGRAMMER.2
unnamed: C3.1, JPMIC.1, R1.2, R5.2, U1.7 (VCC)
unnamed: JPLCD.1, LCD.2
unnamed: C1.1, C5.1, IC1.2 (VO), JPWR.2
RESET: PROGRAMMER.5, R1.1, U1.1 (PC6(/RESET))
SCK: PROGRAMMER.3, U1.19 (PB5(SCK))
SCL: LCD.4, TPSCL.TP, U1.28 (PC5(ADC5/SCL))
SDA: LCD.3, TPSDA.TP, U1.27 (PC4(ADC4/SDA))
VCC: JPH.1, JPLCD.2, JPMIC.2, JPPRG.1, JPW.1, JPWR.1
VIN: C4.1, G1.+, IC1.1 (VI)
WGHT_SIG: HX711.3, TPW.TP, U1.26 (PC3(ADC3))

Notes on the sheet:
Weight Sensor Conn.
Humidity Sensor Conn.
LCD Conn.
Power Regulator
FilaMint
4.0
C. Nhim, D. Hernandez, S. Sapkota, N. Rebolledo
Group 4
VOUT
Microcontroller Test LEDs

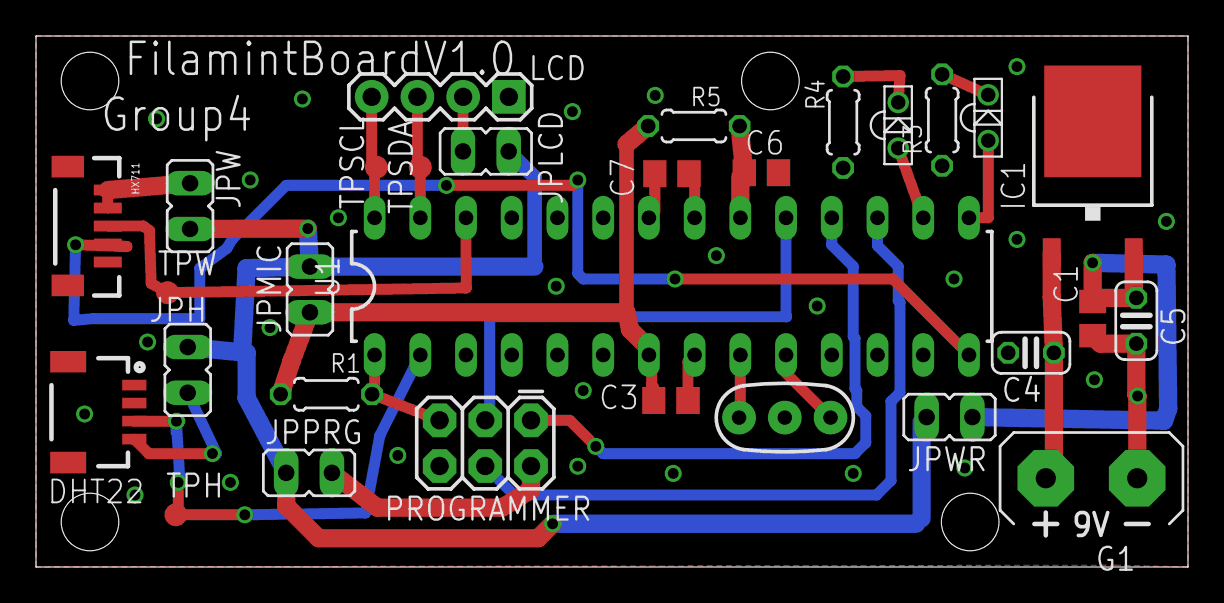
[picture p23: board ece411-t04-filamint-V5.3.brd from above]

Board: 2 copper layers, 64.0 x 29.5 mm, 30 parts (0 on the bottom side), 26 nets.

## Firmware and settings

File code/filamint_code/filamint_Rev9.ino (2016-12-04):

#include <HX711.h>
#include <Adafruit_RGBLCDShield.h>
#include <Adafruit_Sensor.h>

/********************
This program will display a menu for the user. It will display the menu options
and be able to change the backlight color (including shutting the screen off the save battery life).
This program will also include button interaction with the user.

FilaMint, 2016
Portland State University

 ********************/

//This will inlcude the library to the arduino
#include <Wire.h>
#include <Adafruit_RGBLCDShield.h>
#include <utility/Adafruit_MCP23017.h>
#include <math.h>


//The shield uses I2C pins
Adafruit_RGBLCDShield lcd = Adafruit_RGBLCDShield();

//These definitions are for the color
#define OFF 0x0
#define RED 0x1
#define BLUE 0x4
#define WHITE 0x7

//defining buttons of the LCD 

//#define btnRIGHT  0
//#define btnUP     1
//#define btnDOWN   2
//#define btnLEFT   3
//#define btnSELECT 4

#include "DHT.h"
#define DHTPIN 2
#define DHTTYPE DHT22
DHT dht(DHTPIN, DHTTYPE);

//weight
HX711 scale(A1, A0);    // parameter "gain" is ommited; the default value 128 is used by the library


void setup()
{
  //Debugging output
  Serial.begin(9600);
  // The LCDs # columns and # rows
  lcd.begin(12,2);
  dht.begin();

  // weight
  // by the SCALE parameter (not set yet)  

  scale.set_scale(2280.f);     // this value is obtained by calibrating the scale with known weights; see the README for details
  scale.tare();                // reset the scale to 0
  
  lcd.clear();
  lcd.print("New reading");
  lcd.setCursor(0,1);
  lcd.print("Insert new spool");
}

//unsigned integer of 8 bits length
uint8_t i=0;

const int button = 4;   // Number of buttons
int buttonState = 0;    // Variable for reading button status

void loop()
{
  //set the cursor to column 0, line 1
  lcd.setCursor(0,1);
  
  //checks for button press
  uint8_t buttons = lcd.readButtons();
  buttonState = digitalRead(buttons);
  if (buttons & BUTTON_SELECT)
  {
    lcd.clear();
    lcd.print("New reading");
    lcd.setCursor(0,1);
    lcd.print("Insert new spool");
  }
  else if (buttons & BUTTON_DOWN)
  {
    lcd.clear();
    lcd.setCursor(0,0); 
    lcd.print("PLA");
    lcd.setCursor(0,1);
    lcd.print("ABS");
    delay(5000);
    if (buttons & BUTTON_DOWN)
    {
      lcd.clear();
      lcd.setCursor(0,0); 
      lcd.print("ABS 1.75mm");
      lcd.setCursor(0,1);
      lcd.print("ABS 3.00mm");
    }
    else if (buttons & BUTTON_UP)
    {
      lcd.clear();
      lcd.setCursor(0,0); 
      lcd.print("PLA 1.75mm");
      lcd.setCursor(0,1);
      lcd.print("PLA 3.00mm");
    }
  }

  else if(buttons & BUTTON_UP)
  {
    lcd.clear();
    lcd.setCursor(0,0);
    lcd.setBacklight(WHITE);
    // Wait a few seconds between measurements.
    delay(2000);  

    // Reading temperature or humidity takes about 250 milliseconds!
    // Sensor readings may also be up to 2 seconds 'old' (its a very slow sensor)
    float h = dht.readHumidity();
    // Read temperature as Celsius (the default)
    // Check if any reads failed and exit early (to try again).
    if (isnan(h))
    {
      Serial.println("Failed to read from DHT sensor!");
      return;
    }

    // uncomment humidity 
    //move cursor to next line to show both readings
    lcd.clear();
    lcd.print("Humidity: ");
    lcd.print(h);

    lcd.setCursor(0,1);
    lcd.print("Weight: ");
    lcd.print(scale.get_units(), 1);

    if (h > 50)
    {  
      // High alarm text
      lcd.clear();
      lcd.print("High! ");
      lcd.print(h);
    }
  } 
}

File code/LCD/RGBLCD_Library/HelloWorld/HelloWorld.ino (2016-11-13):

/*********************

Example code for the Adafruit RGB Character LCD Shield and Library

This code displays text on the shield, and also reads the buttons on the keypad.
When a button is pressed, the backlight changes color.

**********************/

// include the library code:
#include <Wire.h>
#include <Adafruit_RGBLCDShield.h>
#include <utility/Adafruit_MCP23017.h>


// The shield uses the I2C SCL and SDA pins. On classic Arduinos
// this is Analog 4 and 5 so you can't use those for analogRead() anymore
// However, you can connect other I2C sensors to the I2C bus and share
// the I2C bus.
Adafruit_RGBLCDShield lcd = Adafruit_RGBLCDShield();

// These #defines make it easy to set the backlight color
#define RED 0x1
#define YELLOW 0x3
#define GREEN 0x2
#define TEAL 0x6
#define BLUE 0x4
#define VIOLET 0x5
#define WHITE 0x7

void setup() {
  // Debugging output
  Serial.begin(9600);
  // set up the LCD's number of columns and rows: 
  lcd.begin(12, 2);

  // Print a message to the LCD. We track how long it takes since
  // this library has been optimized a bit and we're proud of it :)
  int time = millis();
  lcd.print("Hello, world!");
  time = millis() - time;
  Serial.print("Took "); Serial.print(time); Serial.println(" ms");
  lcd.setBacklight(WHITE);
}

uint8_t i=0;
void loop() {
  // set the cursor to column 0, line 1
  // (note: line 1 is the second row, since counting begins with 0):
  lcd.setCursor(0, 1);
  // print the number of seconds since reset:
  lcd.print(millis()/1000);

  uint8_t buttons = lcd.readButtons();

  if (buttons) {
    lcd.clear();
    lcd.setCursor(0,0);
    if (buttons & BUTTON_UP) {
      lcd.print("UP ");
      lcd.setBacklight(RED);
    }
    if (buttons & BUTTON_DOWN) {
      lcd.print("DOWN ");
      lcd.setBacklight(YELLOW);
    }
    if (buttons & BUTTON_LEFT) {
      lcd.print("LEFT ");
      lcd.setBacklight(GREEN);
    }
    if (buttons & BUTTON_RIGHT) {
      lcd.print("RIGHT ");
      lcd.setBacklight(TEAL);
    }
    if (buttons & BUTTON_SELECT) {
      lcd.print("SELECT ");
      lcd.setBacklight(VIOLET);
    }
  }
}

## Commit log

2016-10-30 LCD shield info
    PDF with assembly and example code reference
2016-10-30 FilaMint LCD Arduino Code
    This is the code for the LCD display
2016-10-30 Arduino LCD Code REV 2
2016-10-30 Schematic
    V3
2016-11-03 Add files via upload
    I dont know what the leds do
    [Filamint Schematic V4.1.sch]
2016-11-03 Rename Filamint Schematic V4.1.txt to Filamint Schematic V4.1_BOM.txt
2016-11-03 Rev4
    I added some testpoints, jumpers, values to connectors (so ERC pass) and moved the connectors to one side. It passes ERC with 2 approves!
    [Filamint Schematic V4.3.sch]
2016-11-03 Add files via upload
    grouped the LEDs
    [Filamint Schematic V4.4.sch]
2016-11-05 Update and rename load_Cell_to_hx711.txt to hx711 board connection.txt
2016-11-05 organization
    added folders
    [Filamint Schematic V3.1.sch, Filamint Schematic V4.1.sch, Filamint Schematic V4.3.sch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]
2016-11-07 Rename Filamint Schematic V4.1.txt to Filamint Schematic V4.1 BOM.txt
2016-11-10 v4.5
    changed batt, microprosser footprint
    [Filamint Schematic V4.5.brd, Filamint Schematic V4.5.sch]
2016-11-10 very*very* rough draft
    [Filamint Schematic V4.5.brd, Filamint Schematic V4.5.sch]
2016-11-10 draft2-v.4.6
    fixed gnd plane and missing reset connection
    [ece411-t04-filamint-V4.6.brd, ece411-t04-filamint-V4.6.sch]
2016-11-14 all sensors
2016-11-14 Update and rename arduino_conn.md to Readme.md
2016-11-14 Rename hx711 board connection.txt to code/weight/hx711 board connection.txt
2016-11-16 made changes that andrew suggested
    thicker powerlines, rearrange closer
    [ece411-t04-filamint-V4.6.1.brd, ece411-t04-filamint-V4.6.1.sch]
2016-11-16 after meeting with andrew
    final version
    [ece411-t04-filamint-V5.brd, ece411-t04-filamint-V5.sch]
2016-11-17 minor changes
    widen some vcc lines, bigger mounting holes 3.2mm
    [ece411-t04-filamint-V5.1.brd, ece411-t04-filamint-V5.1.sch]
2016-11-17 added bottom silk
    getting error on OSH park saying no bottom silk
    [ece411-t04-filamint-V5.2.brd, ece411-t04-filamint-V5.2.sch]
2016-11-17 Submitted to OSH Park
    added one via for more copper filling
    [ece411-t04-filamint-V5.3.brd, ece411-t04-filamint-V5.3.sch]
2016-11-28 BOM sorted by value
2016-12-03 Add files via upload
    Added functions for the buttons:
    Left: ABS filament selection
    Right: PLS button selection
    Up: Humidity and weight display
    Select: Main screen
2016-12-03 Add files via upload
    Adding button functions
    Up: Humidity and weigh readings
    Left: ABS type filament selection
    Right: PLA type filament selection
    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
2016-12-04 pin update
2016-12-04 added references to filamint board
2016-12-04 pin assignment update
2016-12-04 pin assignment
2016-12-04 load sensor connection pictures
2016-12-04 Add files via upload
    Filamint laser cutting lid and bottom.
    Make sure 2 pieces (lid, bottom). The dimensions need to be 10" x 4.5".
2016-12-04 pins adjusted
    shorted pin 2 and 4 for humidity signal
    [filamint_Rev10.ino]
2016-12-05 arduino 328p pinout
2016-12-06 Now errors if humidity no connected
    [filamint_Rev10.ino]
2016-12-08 Add files via upload
    David, here is the stl file for 3d printing.
    -Colleen
    [thru-swivel_with_rings.stl]
2016-12-08 laser cutting case pt 1
2016-12-08 organization
    moving files around
    [Filamint Schematic V3.1.sch, Filamint Schematic V4.1.sch, Filamint Schematic V4.3.sch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]

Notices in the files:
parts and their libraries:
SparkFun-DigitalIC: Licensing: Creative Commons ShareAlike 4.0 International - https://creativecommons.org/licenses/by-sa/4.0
